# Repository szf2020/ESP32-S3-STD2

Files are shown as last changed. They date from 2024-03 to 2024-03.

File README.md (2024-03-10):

# ESP32-S3-STD2

ESP32-S3-STD2 is a closed-loop controller based on the ESP32-S3 series. A TMC2209 dev board can be connected to control a stepper motor. An on-board encoder provides feedback for precise position control and an addressable RGB LED adds a visual feature for debugging. The board can be attached to the back of a Nema 17 Stepper motor.<br>

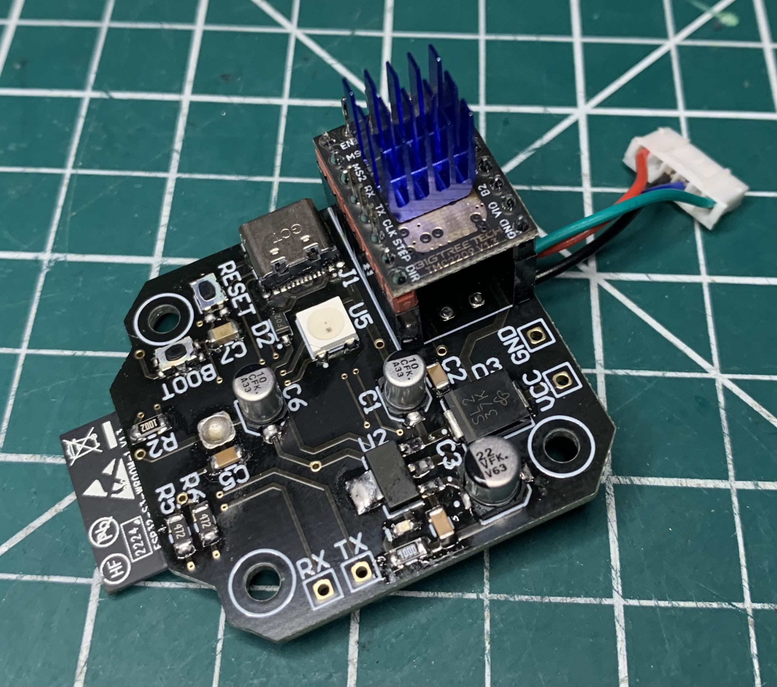
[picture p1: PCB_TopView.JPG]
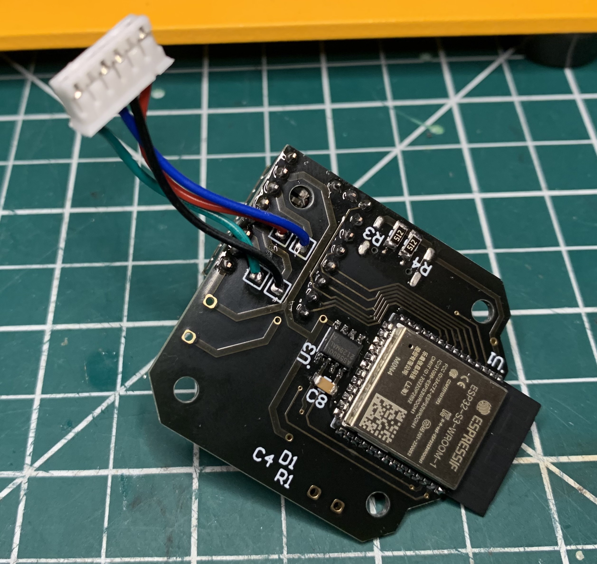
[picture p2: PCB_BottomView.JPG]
&nbsp;&nbsp;&nbsp;&nbsp;&nbsp;&nbsp;&nbsp;&nbsp;&nbsp;&nbsp;&nbsp;&nbsp;&nbsp;&nbsp;<br>

&nbsp;<br>
### ESP32-S3-WROOM-1-N4 MCU

The ESP32-S3-WROOM-1-N4 is an MCU with WiFi 802.11n and Bluetooth LE capabilities. It has a full-speed USB 2.0 OTG which reduces the amount of components needed.<br>

&nbsp;<br>
### AS5600L Hall-effect Encoder

The AS5600L is a magnetic rotary position sensor and is used with a radial magnet. This sensor has a high-resolution 12-bit I²C or PWM output. The AS5600L can be used for precise position control of the stepper motor.<br>

&nbsp;<br>
### WS2812B Addressable LED

WS2812B is an addressable LED that has a control circuit and RGB chip integrated. This visual feature is useful for debugging and testing the basic functionalities of the circuit board.<br>

&nbsp;<br>
### TMC2209 Stepper Driver
Headers are present on the board to connect a TMC2209 dev board or an equivalent. ESP32-S3-STD3 has been successfully tested with a BigTreeTech TMC2209 V1.3 board. This module can be controlled with UART.<br>

&nbsp;<br>
### AZ1117 3.3V Regulator
This SMD 3.3V regulator powers the ESP32 and the other components. The board is powered by either the V-BUS (5Vdc) of the USB-C or the VCC connection for the motor (Maximum 15Vdc). If both supplies are connected at the same time, the highest voltage rules.<br>

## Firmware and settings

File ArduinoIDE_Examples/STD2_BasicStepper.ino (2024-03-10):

#include "FastLED.h"     // WS2812B addressable GRB LED
#include "AS5600.h"      // AS5600L absolute encoder
#include "Wire.h"        // AS5600L uses I2C
#include "TMCStepper.h"  // TMC2209 Stepper motor driver

// Define for AS5600L
#define SDA_PIN    2  // I2C pins are map to any GPIO
#define SCL_PIN    1

// Define for OnBoard WS2812B LED
#define LED_DIN        9   // Data In pin
#define LED_PWR        10  // VDD pin
#define LED_NB         1   // Quanity of LEDs
#define LED_BRT        20  // LED Brightness
#define LED_TYPE       WS2812B
#define COLOR_ORDER    GRB
#define DarkBlue       0x01244a  // Looks turquoise with low brigthness
#define Blank          CRGB(0, 0, 0)

// Define for OnBoard TMC2209 Driver
#define TMC_EN        7    // TMC enable pin   
#define TMC_DIR       16   // TMC dir pin
#define TMC_STEP      15   // TMC step pin  
#define U1RXD         5    // Serial1 RX pin
#define U1TXD         4    // Serial1 TX pin
#define DRIVER_ADDRESS      0b00   // TMC2209 Driver address according to MS1 and MS2
#define R_SENSE             0.11f  // 0.110 Ohms
#define TMC_maxSpeed        778
#define TMC_minSpeed        156
#define moveBufferLength    3
#define moveDelay           200    // milliseconds. Time between move.
#define SERIAL_PORT         Serial1
#define SERIAL_BAUDRATE     115200

CRGB LED[LED_NB];
AS5600L _AS5600L;
TMC2209Stepper TMCdriver(&SERIAL_PORT, R_SENSE, DRIVER_ADDRESS);

// Using with millis() to avoid delay() stoping the program
static uint32_t timeLED = 0;
static uint32_t timeAS5600L = 0;
static uint32_t timeTMCdriver = 0;
static uint32_t timeMove = 0;

bool     statusLED = false;  // Keeps track of LED's on/off state
bool     shaftDir = true;
uint32_t actualSpeed;
int32_t  position;
int32_t  lastPosition;
int32_t  revolutions;
float    angle;
float    displacement;
uint8_t  stepperMoveSelect;  // Use to select the angle in stepperMoveBuffer
uint8_t  stepperMoveStatus;  // Varies between 0 and 2
                             // 0: Delay finish, setting next destination angle.
                             // 1: Destination angle reach, starting delay.
                             // 2: In delay, waiting for it to end.

// Angle the stepper moves to in a loop
float stepperMoveBuffer[moveBufferLength] = {360.00, 180.00, 45.00};

void printTime(void);
void stepperMoveToAngle(float finalAngle);

void setup() {
  Serial.begin(SERIAL_BAUDRATE);
  Serial.println("[ESP32-S3] Setup Configuration...");
  SERIAL_PORT.begin(SERIAL_BAUDRATE, SERIAL_8N1, U1RXD, U1TXD); // Mapping UART1's pins. Not using default ones.

  // TMC2209 Stepper Driver
  pinMode(TMC_EN, OUTPUT);
  digitalWrite(TMC_EN, LOW);
  pinMode(TMC_STEP, OUTPUT);
  pinMode(TMC_DIR, OUTPUT);
  TMCdriver.begin();
  TMCdriver.toff(5);  // Enables driver in software
  //TMCdriver.rms_current(800);
  TMCdriver.microsteps(2);
  TMCdriver.en_spreadCycle(false);
  TMCdriver.pwm_autoscale(true);
  TMCdriver.shaft(shaftDir);

  // WS2812B GRB LED
  pinMode(LED_PWR, OUTPUT);
  digitalWrite(LED_PWR, HIGH);
  FastLED.addLeds<LED_TYPE, LED_DIN, COLOR_ORDER>(LED, LED_NB);
  FastLED.setBrightness(LED_BRT);

  // AS5600L Magnetic Encoder
  Wire.begin(SDA_PIN, SCL_PIN);
  _AS5600L.begin(8); // Set dir pin. Dir pin is connected to GND. Pin 8 is not connected and only use for the begin().
  if(_AS5600L.isConnected()) Serial.println("[AS5600L] Connected.");
  _AS5600L.getCumulativePosition();
  _AS5600L.resetPosition(); // Set current position as initial position
  printTime();
  Serial.println("[AS5600L] Setting current position as initial position.");
  printTime();
  Serial.print("[AS5600L] Cumulative Position: ");
  Serial.print(position);
  Serial.print("\tRevolutions: ");
  Serial.println(revolutions);
}

void loop() {
  // LED ON every 1000ms
  if((millis() - timeLED) >= 1000){
    timeLED = millis();
    LED[0] = DarkBlue;
    FastLED.show();
    statusLED = true;
    //printTime();
    //Serial.println(" | [WS2812B] State: ON");
  }

  // LED OFF after being ON for 100ms
  if(statusLED == true){
    if((millis() - timeLED) >= 100){
      timeLED = millis();
      LED[0] = Blank; // Off
      FastLED.show();
      statusLED = false;
      //printTime();
      //Serial.println(" | [WS2812B] State: OFF");
    }
  }

  if(millis() - timeAS5600L >= 10){
    timeAS5600L = millis();
    position = _AS5600L.getCumulativePosition();
    revolutions = _AS5600L.getRevolutions();  // Cumulative Position is divided by 4096
    angle = (float(position) * float(360)) / float(12288);
    stepperMoveToAngle(stepperMoveBuffer[stepperMoveSelect]);
  }

  // Print position to serial if it changes
  if((lastPosition < (position-1)) || (lastPosition > (position+1))){
    lastPosition = position;
    printTime();
    Serial.print("[AS5600L] Cumulative Position: ");
    Serial.print(position);
    Serial.print("\tRevolutions: ");
    Serial.print(revolutions);
    Serial.print("\tAngle: ");
    Serial.println(angle);
  }
}

void printTime(void){
  int mSeconds = millis()%1000;
  int seconds = (millis()/1000)%60;
  int minutes = (millis()/60000)%60;
  char buffer[64];
  sprintf(buffer, "%dmin %ds %dmS | ", minutes, seconds, mSeconds);
  Serial.print(buffer);
}

void stepperMoveToAngle(float finalAngle){
  if((finalAngle >= (angle-0.3)) && (finalAngle <= (angle+0.3))){ // Accuracy of +/-0.3 degree
    TMCdriver.VACTUAL(0);
    if(stepperMoveStatus == 0){
      stepperMoveStatus = 1;  // Destination angle reach, ready to start delay.
    }else if(stepperMoveStatus == 1){
      timeMove = millis();
      stepperMoveStatus = 2; // Delay as been start, waiting.
    }else if(stepperMoveStatus == 2){
      if(millis() - timeMove >= moveDelay){
        stepperMoveStatus = 0; // Delay ended, ready to load next destination angle
        stepperMoveSelect++;
        stepperMoveSelect %= moveBufferLength;
      }
    }
    printTime();
    char buffer[128];
    sprintf(buffer, "[ESP32-S3] Destination angle of %f degrees reach.\tAccurate current angle: %f", finalAngle, angle);
    Serial.println(buffer);
  }
  else if(finalAngle <= (angle-0.3)){ // Accuracy of +/-0.3 degree
    shaftDir = false;
    TMCdriver.shaft(shaftDir);
    displacement = angle - finalAngle;
    if((displacement/10) >= 5){
      if(actualSpeed >= TMC_maxSpeed){
        actualSpeed = TMC_maxSpeed;
      }else{
        actualSpeed += TMC_minSpeed/3;
      }
      if(actualSpeed < TMC_minSpeed){
        actualSpeed = TMC_minSpeed;
      }
      TMCdriver.VACTUAL(actualSpeed);
    }else if((displacement/10) < 5){
      actualSpeed = (TMC_maxSpeed/5)*(displacement/10);
      if(actualSpeed > TMC_minSpeed){
        TMCdriver.VACTUAL(actualSpeed);
      }else{
        TMCdriver.VACTUAL(TMC_minSpeed);
      }
    }
  }
  else if(finalAngle >= (angle+0.3)){ // Accuracy of +/-0.3 degree
    shaftDir = true;
    TMCdriver.shaft(shaftDir);
    displacement = finalAngle - angle;
    if((displacement/10) >= 5){
      if(actualSpeed >= TMC_maxSpeed){
        actualSpeed = TMC_maxSpeed;
      }else{
        actualSpeed += TMC_minSpeed/3;
      }
      if(actualSpeed < TMC_minSpeed){
        actualSpeed = TMC_minSpeed;
      }
      TMCdriver.VACTUAL(actualSpeed);
    }else if((displacement/10) < 5){
      actualSpeed = (TMC_maxSpeed/5)*(displacement/10);
      if(actualSpeed > TMC_minSpeed){
        TMCdriver.VACTUAL(actualSpeed);
      }else{
        TMCdriver.VACTUAL(TMC_minSpeed);
      }
    }
  }
}

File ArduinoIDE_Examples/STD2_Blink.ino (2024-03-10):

#include <FastLED.h>

// Define for on-board WS2812B LED (Pinout)
#define LED_DIN          9
#define LED_PWR          10
#define LED_NB           1
#define LED_BRT          20
#define LED_TYPE         WS2812B
#define COLOR_ORDER      GRB

CRGB LED[LED_NB];

bool LED_STATE = false;  // Used to know if the LED is ON or OFF

void setup() {
  Serial.begin(115200);
  Serial.print("Setup Configuration...");

  pinMode(LED_PWR, OUTPUT);
  digitalWrite(LED_PWR, HIGH);

  FastLED.addLeds<LED_TYPE, LED_DIN, COLOR_ORDER>(LED, LED_NB);
  FastLED.setBrightness(LED_BRT);
}

void loop() {
  static uint32_t lastTime = 0;

  if((millis() - lastTime) >= 1000){
    lastTime = millis();
    LED[0] = 0x01244a;  // Dark Blue Sky
    FastLED.show();
    LED_STATE = true;
    Serial.println("LED STATE: ON");
  }

  if(LED_STATE == true){
    if((millis() - lastTime) >= 100){
      lastTime = millis();
      LED[0] = CRGB(0, 0, 0); // Off
      FastLED.show();
      LED_STATE = false;
      Serial.println("LED STATE: OFF");
    }
  }
}
